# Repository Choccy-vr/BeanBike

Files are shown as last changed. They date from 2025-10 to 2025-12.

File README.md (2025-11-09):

# BeanBike

A DIY smart eBike display and controller.

## Why?

I made this because I really like eBikes; they are just fun. I have always wanted my own, but off the shelf they are way too expensive. So I thought of going the custom route, making my own controller. But then I thought, if I am really going to do this, I am not going to get some normal boring eBike I want my eBike. And that is how this came to be.

## Pictures!

### PCBs

#### Controller

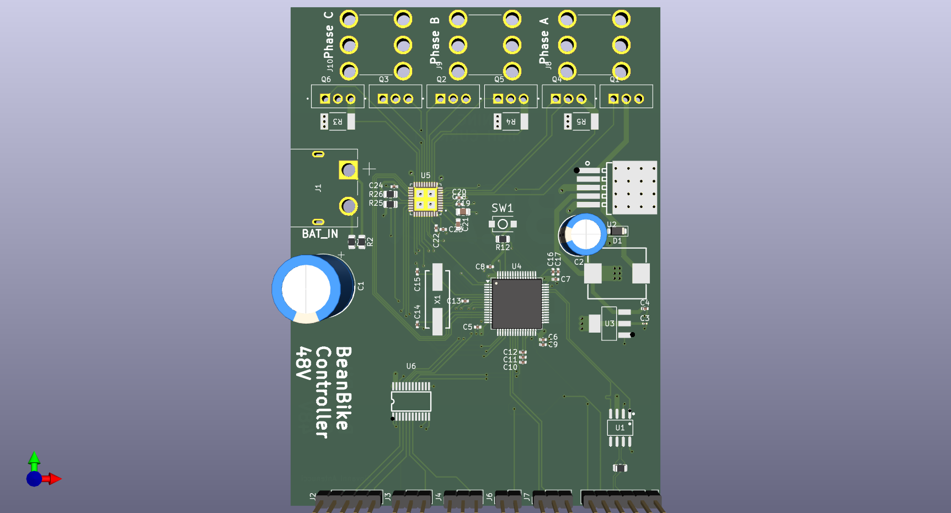
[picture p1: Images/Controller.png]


#### Display

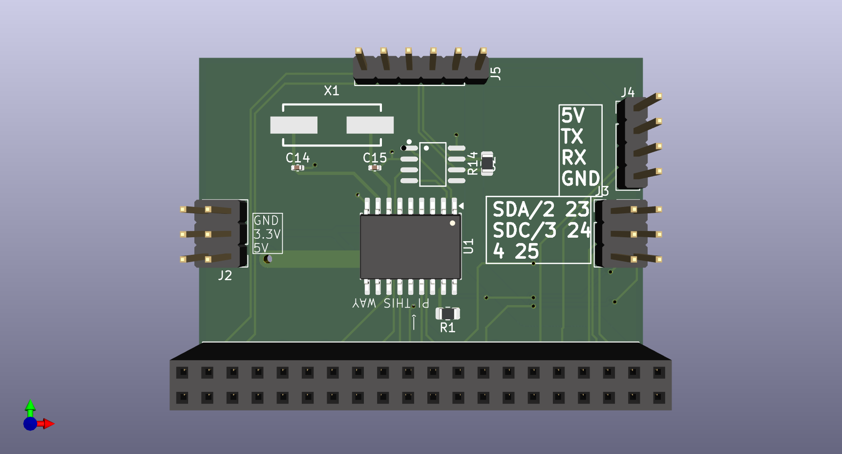
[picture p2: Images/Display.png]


## BOM

|Product Name |Product Description |Product Link |Product unit price|Product amount|Product Cost|Total (Before Tax + Shipping)|Total (Without Shipping)|Total  |
|---|---|---|---|---|---|---|---|---|
|Display-PCB |PCB for display |https://jlcpcb.com/ |4.12 |5 |$20.58 |$198.40 |$212.29 |$259.05|
|2x20 Socket |Socket for Pi |https://www.digikey.com/en/products/detail/sullins-connector-solutions/SFH11-PBPC-D20-ST-BK/1990093 |1.52 |1 |$1.52 | | | |
|2x3 Header |Expansion Pins |https://www.digikey.com/en/products/detail/sullins-connector-solutions/PBC03DAAN/861061 |0.58 |2 |$1.16 | | | |
|Display |Display for eBike |https://www.waveshare.com/product/displays/lcd-oled/lcd-oled-2/3.5inch-480x800-lcd.htm |44.99 |1 |$44.99 | | | |
|Mini-HDMI to HDMI Cable|HDMI cable for display |https://www.aliexpress.us/item/3256809615077123.html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 |1.99 |1 |$1.99 | | | |
|Micro USB to USB C |USB cable for display |https://www.amazon.com/DteeDck-Adapter-Braided-Charging-Transmission/dp/B0BD36TZBK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 |5.49 |1 |$5.49 | | | |
|Controller-PCB |PCB for controller |https://jlcpcb.com/ |11.77 |5 |$58.87 | | | |
| | | | | | | | | |
|CSS2H-2512R-1L00F |Shunt Resistors |https://www.digikey.com/en/products/detail/bourns-inc/CSS2H-2512R-1L00F/6023764 |1.27 |3 |$3.81 | | | |
| | | | | | | | | |
|PAS sensor |Pas Sensor |https://www.aliexpress.us/item/3256808182150916.html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 |1.99 |1 |$1.99 | | | |
|Throttle sensor |Twist Throttle Handle |https://www.aliexpress.us/item/3256806514034716.html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 |1.99 |1 |$1.99 | | | |
|Brake sensor |Brake/shut off sensor |https://www.aliexpress.us/item/3256805985764030.html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 |5.9 |1 |$5.90 | | | |
|MOSFET Heatsinks |Heatsink for MOSFETs |https://www.aliexpress.us/item/3256803892794950.html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 |0.2 |10 |$1.99 | | | |
|M8 Connector 2P |Connector for brake sensor |https://www.aliexpress.us/item/3256805115817349.html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 |2.97 |1 |$2.97 | | | |
|M8 Connectors 3P |Connectors for PAS and Throttle|https://www.aliexpress.us/item/3256805115817349.html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 |1.75 |4 |$6.99 | | | |
|M8 Connector 6P |Connector for Display |https://www.aliexpress.us/item/3256805115817349.html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 |3.46 |1 |$2.97 | | | |
|MOSFETs |MOSFETs |https://www.digikey.com/en/products/detail/infineon-technologies/IRFB4110PBFXKMA1/22157630 |3.06 |6 |$18.36 | | | |
|Capacitor 680uF |big cap for controller |https://www.digikey.com/en/products/detail/chemi-con/EKZN630ELL681MK30S/4843904 |1.53 |1 |$1.53 | | | |
|Capacitor 330uF |big cap for controller |https://www.digikey.com/en/products/detail/rubycon/25ZLJ330M8X11-5/3134207 |0.54 |1 |$0.54 | | | |
|Screw Terminal |Phase Connector |https://www.digikey.com/en/products/detail/keystone-electronics/8196/316832 |1.24 |3 |$3.72 | | | |
|Ring Connector |Phase Wire connector |https://www.digikey.com/en/products/detail/molex/0191930245/1952714 |0.53 |3 |$1.59 | | | |
|GPS module |GPS module |https://www.aliexpress.us/item/3256806636967867.html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|6.39 |1 |$6.39 | | | |
|M8 Connector 5P |Connector for ENCODER |https://www.aliexpress.us/item/3256805115817349.html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 |3.06 |1 |$3.06 | | | |

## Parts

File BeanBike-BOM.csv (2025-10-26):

Product Name | Product Description | Product Link | Product unit price | Product amount | Product Cost | Total (Before Tax + Shipping) | Total (Without Shipping) | Total | Estimated Total with GPS
Display-PCB | PCB for display | https://jlcpcb.com/ | 0.64 | 5 | $3.20 | $188.25 | $201.43 | $235.39 | $260-270
2x20 Socket | Socket for Pi | https://www.digikey.com/en/products/detail/sullins-connector-solutions/SFH11-PBPC-D20-ST-BK/1990093 | 1.52 | 1 | $1.52
2x3 Header | Expansion Pins | https://www.digikey.com/en/products/detail/sullins-connector-solutions/PBC03DAAN/861061 | 0.58 | 2 | $1.16
Display | Display for eBike | https://www.waveshare.com/product/displays/lcd-oled/lcd-oled-2/3.5inch-480x800-lcd.htm | 44.99 | 1 | $44.99
Mini-HDMI to HDMI Cable | HDMI cable for display | https://www.aliexpress.us/item/3256809615077123.html?curPageLogUid=s5fbXvPEQDyt | 1.99 | 1 | $1.99
Micro USB to USB C | USB cable for display | https://www.amazon.com/DteeDck-Adapter-Braided-Charging-Transmission/dp/B0BD36TZBK | 5.49 | 1 | $5.49
Controller-PCB | PCB for controller | https://jlcpcb.com/ | 6.96 | 5 | $34.80
Controller-PCBA | PCBA for controller PCB | https://jlcpcb.com/ | 29.2 | 2 | $58.40
CSS2H-2512R-1L00F | Shunt Resistors | https://www.digikey.com/en/products/detail/bourns-inc/CSS2H-2512R-1L00F/6023764 | 1.27 | 3 | $3.81
ESP32-WROOM-32E-N8 | Microcontroller for controller | https://www.digikey.com/en/products/detail/espressif-systems/ESP32-WROOM-32E-N8/13159522 | 5.28 | 1 | $5.28
PAS sensor | Pas Sensor | https://www.aliexpress.us/item/3256808182150916.html?mp=1 | 1.99 | 1 | $1.99
Throttle sensor | Twist Throttle Handle | https://www.aliexpress.us/item/3256809866650629.html?curPageLogUid=YqcZ7PjFSbH2 | 4.8 | 1 | $4.80
Brake sensor | Brake/shut off sensor | https://www.aliexpress.us/item/3256805985764030.html?curPageLogUid=UFPqvqSYBL2c | 5.9 | 1 | $5.90
MOSFET Heatsinks | Heatsink for MOSFETs | https://www.aliexpress.us/item/3256803892794950.html?curPageLogUid=eevL79xpdQiV | 0.2 | 10 | $1.99
M8 Connector 2P | Connector for brake sensor | https://www.aliexpress.us/item/3256805115817349.html?mp=1 | 2.97 | 1 | $2.97
M8 Connectors 3P | Connectors for PAS and Throttle | https://www.aliexpress.us/item/3256805115817349.html?mp=1 | 1.75 | 4 | $6.99
M8 Connector 6P | Connector for Display | https://www.aliexpress.us/item/3256805115817349.html?mp=1 | 3.46 | 1 | $2.97

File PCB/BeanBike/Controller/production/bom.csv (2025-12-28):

Designator | Footprint | Quantity | Value | LCSC Part #
C1 | CP_Radial_D12.5mm_P5.00mm | 1 | 680uF 63V
C10, C12, C13, C16, C5, C6, C7, C8 | 0402 | 8 | 100nf | C1525
C11, C17, C20, C22, C23 | 0402 | 5 | 1uF | C52923
C14, C15 | 0402 | 2 | 30pF | C1570
C18, C24 | 0402 | 2 | 0.1uF | C1525
C19 | 0805 | 1 | >10uF | C45783
C2 | CP_Radial_D8.0mm_P3.50mm | 1 | 330uF 25V
C21 | 0603 | 1 | 47nF | C1622
C3 | 0201 | 1 | 22uF | C59461
C4 | 0402 | 1 | 10uf | C15525
C9 | 0402 | 1 | 4.7uF | C1569
D1 | D_SOD-123F | 1 | D | C64898
D10 | D_SMA | 1 | 3.3v Zener | C19077475
D2, D4, D5, D6 | 0603 | 4 | LED | C2286
D3 | 0805 | 1 | LED | C2297
D7 | 0603 | 1 | LED | C2296
D8 | 0603 | 1 | LED | C2290
D9 | D_SMA | 1 | 5v Zener | C19077477
F1 | FUS_RKEF300_TYCO_TYC | 1 | 5v Polyfuse
F2 | FUSE_MF_R065_2_BRN | 1 | 3.3v Polyfuse
J1 | MountingHole_3.2mm_M3_Pad_Via | 1 | XT60 +
J10 | KEYSTONE_8196 | 1 | PHASE C
J11 | MountingHole_3.2mm_M3_Pad_Via | 1 | XT60 -
J2 | PinHeader_1x05_P2.54mm_Vertical | 1 | Conn_01x05_Pin
J3 | PinHeader_1x03_P2.54mm_Vertical | 1 | Throttle Conn
J4 | PinHeader_1x03_P2.54mm_Vertical | 1 | PAS Conn
J5 | PinHeader_1x06_P2.54mm_Vertical | 1 | Display Conn
J6 | PinHeader_1x02_P2.54mm_Vertical | 1 | Brake Conn
J7 | PinHeader_1x06_P2.54mm_Vertical | 1 | ST-Link-Debug
J8 | KEYSTONE_8196 | 1 | PHASE A
J9 | KEYSTONE_8196 | 1 | PHASE B
L1 | IND-SMD_L11.6-W10.1 | 1 | CYA1040-33UH | C6364680
Q1 | TO254P1050X476X2020-3 | 1 | PHASE A HIGH
Q2 | TO254P1050X476X2020-3 | 1 | PHASE B HIGH
Q3 | TO254P1050X476X2020-3 | 1 | PHASE C HIGH
Q4 | TO254P1050X476X2020-3 | 1 | PHASE A LOW
Q5 | TO254P1050X476X2020-3 | 1 | PHASE B LOW
Q6 | TO254P1050X476X2020-3 | 1 | PHASE C LOW
R1, R12 | 0805 | 2 | 10k | C17414
R10, R6, R8, R9 | 0805 | 4 | 15k | C17475
R11, R13 | 0805 | 2 | 1k | C17513
R14 | 0805 | 1 | 120 | C17437
R2 | 0805 | 1 | 180k | C17501
R25, R26 | 0805 | 2 | 73k | C17819
R3, R4, R5 | RES_1L00x_BRN | 3 | CSS2H-2512R-1L00F | C4175647
R7 | 0805 | 1 | 330 | C17630
SW1 | SW-SMD_L3.9-W3.0-P4.45 | 1 | SW_Push | C720477
U1 | SOIC-8_L4.9-W3.9-P1.27-LS6.0-BL | 1 | SN65HVD230DR | C12084
U2 | PG-TO-263-5_L10.2-W8.7-P1.70-LS14.4-BR | 1 | TD1501HS50 | C134490
U3 | SOT-223-3_L6.5-W3.4-P2.30-LS7.0-BR | 1 | AMS1117-3.3 | C6186
U4 | LQFP-64_10x10mm_P0.5mm | 1 | STM32G473RETx | C730120
U5 | QFN50P600X600X80-41N | 1 | DRV8353SRTAT | C2150480
U6 | TSSOP-24_L7.8-W4.4-P0.65-LS6.4-BL | 1 | SN74LVC4245APWR | C7859
X1 | CRYSTAL-SMD_L11.5-W4.8-LS12.7 | 1 | X49SM8MSD2SC | C12674

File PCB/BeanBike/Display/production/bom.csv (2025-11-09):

Designator | Footprint | Quantity | Value | LCSC Part #
C14, C15 | 0402 | 2 | 30pF | C1570
J1 | PinSocket_2x20_P2.54mm_Vertical | 1 | Pi 0 2W
J2 | PinHeader_2x03_P2.54mm_Vertical | 1 | Power Conn
J3 | PinHeader_2x03_P2.54mm_Vertical | 1 | Data Conn
J4 | PinHeader_1x04_P2.54mm_Vertical | 1 | GPS/DEBUG
J5 | PinHeader_1x06_P2.54mm_Vertical | 1 | Display Conn
R1 | 0805 | 1 | 10k | C17414
R14 | 0805 | 1 | 120 | C17437
U1 | SOIC-18W_7.5x11.6mm_P1.27mm | 1 | MCP2515-xSO | C15193
U2 | SOIC-8_L4.9-W3.9-P1.27-LS6.0-BL | 1 | SN65HVD230DR | C12084
X1 | CRYSTAL-SMD_L11.5-W4.8-LS12.7 | 1 | X49SM8MSD2SC | C12674

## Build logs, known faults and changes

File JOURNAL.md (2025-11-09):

<!--
  ===================    !!READ THIS NOTICE!!   ====================
  DO NOT edit this file manually. Your changes WILL BE OVERWRITTEN!
  This journal is auto generated and updated by Hack Club Blueprint.
  To edit this file, please edit your journal entries on Blueprint.
  ==================================================================
-->

## 10/10/2025 5 PM - Started KiCad Project  

Didn't really do a lot, just started the KiCad Project and labeled all the MCU pins for the controller.



Well, pretty much it, but I need 250 characters, so I will talk about blueprint. I kinda am liking it, it is obviously a continuation of Highway, but I like it. Ngl kinda feels unoriginal, but I still like it. 

It is basically Highway, but with some parts of SoM and more refined.  

## 10/10/2025 8 PM - Finished V1 Power Circuit  

I basically made the schematic for the power supply.

Most of the time was spent researching and seeing what I had to do to make sure it is safe and everything gets what it wants. I am debating getting the Power on a different board, but I don't think I will.
But now I have battery level, 3.3v (MCU), 5v (display), 12v (misc like lights). 
I made a more complex circuit, but then I realized eBike batteries already have a BMS 😭 so I got rid of it.
So far, kinda liking this, but I am dreading the day I have to make a case, especially waterproof :(  

## 10/10/2025 9 PM - Added Connectors  

I went through and did all the tedious work of creating the connectors. 

I was also thinking about the features I am going to add specifically for anti-theft. I want to have enough smart anti-theft features that you don't need to lock your bike up. So I will have things like PIN, Phone detection to make sure you can ride it. To make sure that if you do try to steal it, you won't be able to, I will lock the motor, start an alarm, pretty much cut power, other than to the anti-theft features, oh, and also GPS. So this would be effective, but thieves could still pick it up, take out the battery, and other things so I will probably still carry one around, but for those times when you forget it, then you can still be calm knowing your bike won't get stolen.  

## 10/11/2025 1 PM - Motor Controller  

I finished the Motor connection and etc.

So I used a BLDC motor IC for easy controlling and etc. Honestly I don't get why eBike controller are so expensive this seems down right resonable.
When I brake it will now automatically cut power to the motor no matter what (Hard wired) and I can control it with firmware too. So now I am going to go through and finish a few things then I will test it in a simulation and then I should be good to go to the PCB.  

## 10/11/2025 4 PM - Footprints  

I hate selecting footprints; let's make that clear right now, I hate it.

I ran the ERC and fixed all those problems, and I moved to selecting the footprints. I got a list on Digi-Key for all my parts, but I hate this still. A big, big problem I am facing right now is that I need 3 buck converters for 3.3v, 5v, and 12v. Someone suggested going from 12v to 5v then to 3.3v so I will try that.  

## 10/11/2025 7 PM - 48v -> 24v  

Ok for the past 2 hours I have been working on the buck converters.

Tell me why it is so hard to just go down to a lower voltage doesn't make sense but whatever. I spent1.5 hours trying to make my own but the n I came across a actual life saver [webench.ti.com/power-designer](webench.ti.com/power-designer). I got done my 24v converter and now the rest  

## 10/11/2025 8 PM - Finished V1 Schematic  

I finally finally finished V1 of my motor controller!

You know how earlier I said I don't get why motor controllers are so expensive? Yeah, I take that back. I finished all the conversions and now have 24v, 12v, 5v, and 3.3v available to me, all at around 2.5A. I thought the inductors would've made this huge, but ehh, I am estimating around 100mm by 90mm. Then, to top it all off, I did footprints my favorite.  

## 10/12/2025 3 PM - Started PCB  

I started on the PCB.

I started by grouping the components into sections of the board, like one group for power, one for motor, one for connectors, and one for the MCU. I then combined them into a compact layout, drew my edge cuts, and started plotting traces. I have done most of the power, and now I am on data. The board will have 4 layers, front and back for power, and the middle layers for data. After I finish it, I will probably ask someone to review it because this is my first PCB with a lot of current, and I need it to be safe.  

## 10/12/2025 9:29 PM - Finished V1 PCB  

I finished routing all the PCB, and it should be good!

To be honest, I am not that confident, so that is why I am getting it reviewed by someone a lot smarter than me. This feels really nice to get done. I would say this is the hardest part; it should all be smooth sailing from here. And best of all, software is next! Oh, also, I forgot to run to DRC, guess I have to do that :( I really hate all the repetitive work of making PCBs like it is fun until you get to that part.  

## 10/12/2025 9:48 PM - Quick Update: DRC & Silkscreen  

Quick update: I fixed DRC violations and added silk screen text.  

I don't think I am done with it completely. I still have to add all the part numbers, but really, I already have them picked out; I just need to put them in and generate the BOM and Gerbers. It is easy but repetitive. Welp, see you then  

## 10/14/2025 - PCB v2  

I have done alot of research and getting feedback.

I have gotten feedback on my PCB and how not to burn down my house. I need to majorly increase the track width but I have decided to just up my board to 6 layers and it would be like this. Back:Solid GND In4:PWR_MOTOR then the rest is yet to be decided but that is what is new. Then in v1 signals were being passed from one area to another (mostly at connectors) so I am fixing that. I felt it would be easier to just redo the routing and as a perk I can make it neater.  

## 10/15/2025 - Layout PCB v2  

I have laid out all of PCB v2 this time, taking a lot more care into it.

I have decided to omit the 24V and 12V lines. Really, I had no use for them other than lights, but after seeing how expensive wired-in lights are, I decided against it. The PCB is split into 3 parts now: MCU, Power, and Motor. I am still deciding whether to arrange it vertically or more horizontally, but I am thinking vertically.  

## 10/16/2025 6 PM - Issues  

Well, I laid out my PCB v2, and it's all good, but there is an issue.

So I laid out my PCB, it was all nice and neat, but ... I just now realized that the chip I was using the DRV8308 does not support 48v :(. So I have to replace it. I am replacing it with the DRV8353. It is a newer chip and supports 48v. But I really do not want to change everything.  

## 10/16/2025 9 PM - Updated Motor IC  

So after a lot, I finally got the motor IC all updated.

It was a lot, but I think I finally have this all down, and it feels so nice. One good thing happened, though I had the MOSFETs mixed up, so that would not have been good. I rearranged the GPIOs to make it fit a lot better. I also got to get rid of the level shifters, and I feel it is a lot less complex.  

## 10/18/2025 - PCB v2  

I routed a placed everything on PCB v2 and it should be finished.

Been a while. But I finished everything on PCB v2 (except silkscreen). I placed all the new components updated it and all nice and neat. I added copper fills for connecting my high-power things so I don't have to worry about big traces. But anyway, now I am getting it reviewed once again to make sure it is very good.  

## 10/19/2025 11 AM - Finish PCB v2  

I had a problem with my PCB, but I fixed it, and now v2 is officially finished.

In my PCB, there were some isolated copper islands, so I had to fix that by re-routing some of the PCB. This should be the actual PCB that I send to JLC PCB. Now I'm going to make the firmware, and it shouldn't be too hard. Altough I have never interacted with a SPI device without a library so that will take a bit.  

## 10/19/2025 3 PM - DRV8353 implementation  

I am finally working on firmware!

Right now, I am working on the DRV8353 implementation. I have Fault detection working. For everywhere you see uart.sendData(), that is me sending data to my display (the smart thing) to see what it will decide to do with it. At first, I was a little nervous because I had never read/write raw registries from SPI, but it is kind of easy. Oh, and I also set up an interrupt on the FAULT pin to make sure I catch all faults instantly. Next up is Driver Control.  

## 10/19/2025 8 PM - Finished DRV8353 implementation  

I finished the DRV8353 implementation.

Note, this does not mean that my controller firmware is done, just that the code to interface with the DRV8353 is done. Anyway, I added a bunch of functions to control all the different registries. Next, I have to make the motor control code (PAS, Cruise Control, actually sending PWM signals, getting motor speed, etc.).

## 10/20/2025 - More Firmware  

Yay, more Firmware writing

Anyway, let's first talk about #lounge exploding rn first time it has seen use in forever. Also, why did AWS go down? It was so annoying, I could do basically nothing. But back to my project, I basically just wrote a bunch of code for the firmware. That is it, I am tired and want to go to bed gn.  

## 10/21/2025 - *Finished Firmware  

So I finished the firmware!!

* Well, I sort of did. 
Software is never finished; I can just keep adding and adding, and I plan to. This is just it has enough that it will work, I can always change it. That is the great thing about software. Anyway some of the calculations may be off but this is because I don't have the motor or bike to base it off of. I am going to keep adding to it, but as of now, to the display!

## 10/22/2025 5 PM - Research & Schematic  

So I researched for a while, and I landed on the Pi Zero 2 W.

Most of the time spent on this journal was researching, I couldn't choose what to run my display on, and a display. I needed a ~3.5in display, and SPI just wouldn't really work, so the next abundant option was DSI. But another problem arose, the board I was planning on using, the Pi Zero 2 W, doesn't have DSI. So I was contemplating using a Compute module or using an HDMI display with the zero. I decided to use an HDMI display, even though it is a bit more expensive, it is easily swappable, so if anything ever goes wrong. This PCB isn't a complicated one, not supposed to be, mainly just supposed to organize my board.

## 10/22/2025 7 PM - Display PCB  

So I finished the Display PCB

Again, just re-stating this is not supposed to be a complex PCB, just something to better organize my screen. So with that out of the way, now it is on to the most important part of this, making the customized OS. This custom OS will let me strip down to just what I need, further decreasing boot time, and as a bonus, it makes it seem more professional.  

## 10/25/2025 11 AM - Bike App  

I started work on the Bike app

I think it looks really good. I am just working on the UI now, and functionality will come later. Also, quick update on this, I am really starting my YSWS rn and don't know if I will be able to finish this. I will try, but I might have to cut some things out.  

## 10/25/2025 2 PM - Way too many variables  

I have way way way to many variables.

Like it is absurd to creater this UART script it took 2 hrs of mindless copy and pasting. Anyway I am happy that it is done. I think that I still have to change a few things to make everything work all nice. I have to add a few more things and then v1 of the app will be done. I think since I am starting to get super busy I am going to strip out alot of what I planned but it still would be quite a advanced eBike and then through OTA updates keep adding.

## 10/25/2025 4 PM - Finish up Software  

I finished up the software. 

So I finished up the rest of the app and fixed a few things with the controller firmware. Then I built the firmware, and I tried to build the app turns out you need to be on Linux. So I tried macOS turns out that doesn't count as Linux, so I had to go into Ubuntu and build it there. Surprisingly more complicated than I thought. Anyway, I have it all built, and now I have to get it ready for shipping.

## 10/25/2025 11 PM - Finishing Things Up  

This is by far the most time I have spent on one journal.

This journal was a long one. I got everything ready for shipping. I made all my gerbers and BOMs for my PCB changed a good amount of my parts, just so I can get the PCBA cost down. README, organizing, and more. Always hated this part of hardware. It is always so boring and long. Anyway, I got some feedback that my project is at most a tier 2 and maybe a tier 3. That is not good at all. So I might add a GPS module, one problem with that is that although it will increase the price, something I am already over the tier 2 budget.

## 10/26/2025 - Finished  

Ok so I have finished it! I really wanted to get in GPS but I don't have the budget :(. I really need this to be a tier 2 project at least or some way to get the extra budget I am $35.39 over (which isn't that much) but I don't think I could cover that. I included the estimated price with GPS too just in case there is some way to get it covered. maybe by some miracle I can get tier 1 or some way to get the extra funds covered. I also researched the GPS module if I do get GPS I am going for the MAX-M10M-00B cheapest one I could find that is still well supported and accurate.


## 10/30/2025 - Research Research Research  

Some say research is the thief of all joy.

So, I need to narrow my PCB down to 4 layers, but after **researching**, I noticed a VESC project. Basically, it is an open-source project for motor controllers, firmware, etc., which is great. However, the hardware schematics haven't been updated for a while. Also, while I would know that it would work well, I don't know; something is just wrong with it. It kind of defeats the purpose of doing all of this by myself. So I will probably not copy off of it, but I will take inspiration just to make sure my board is ready for this. Also, I think maybe I might switch to an STM32. I don't like it, but it does make a lot of sense for this project, and I think it is cheaper and smaller than an ESP.  

## 10/31/2025 - Project Journal?  

Well, I finally did it. I started a project journal.


As my projects get more and more advanced, I really need somewhere to document my research, my notes, etc. I am actually finding it very beneficial, plus it makes it seem more professional. Anyway, a lot of stuff happened in this session. I really started to research all of the different things I am doing. Like for the MCU, I am moving away from the ESP32 to the STM32G4. And still researching this, but switching from UART to CAN. I am very excited about it seems like it is a vast step up from UART tbh, no clue why I didn't start with it, mostly because the ESP doesn't have that, and I didn't know a lot about it. Last remark paper has its limits. I want an iPad so bad  

## 11/1/2025 1 PM - Last Bit of Research  

Well, I think I have done enough research to start working on the schematic.

I have chosen new ICs for the buck converters. The LM2596HVS is for 48v to 5v. The TPS5430DDAR is for 5v to 3.3v. These, I feel, are going to help a lot. First of both are an all-in-one package, which is super nice. Then the LM2596HVS can do 3A, so that would also be nice. Both are also a lot less money. More went into it, but that was an overview. So here we go!  

## 11/1/2025 2 PM - PCB v3 Schematic  

I started work on PCB v3!

So I got rid of pretty much all power items to replace them. 5V was pretty easy; I needed an external inductor, which I thought I got rid of, but fine. Also, I changed to TD1501HS50. Then, for 3.3,v I was going to use a buck converter, but I realized I could just use an LDO. So I picked the AMS1117-3.3, and that circuit is very simple. I am now going to the STM32!

## 11/1/2025 8 PM - Simple FOC & Resaerch!  

I recently came across a project called [Simple FOC](https://github.com/simplefoc/Arduino-FOC).

This looks like it will be super nice for me and work pretty easily with my Motor IC and STM32. I also came across this YouTuber [Great Scott](https://www.youtube.com/@greatscottlab). I watched a good amount of his videos to get a better grasp on FOC and Electric Motors.  

## 11/4/2025 - iPad!!!  

It has been a while, but great news, I got an iPad!!!!!


Facebook Marketplace is a lifesaver. So instead of having a physical notebook, I can have a digital one! So I transferred everything from my paper notebook to my iPad. 
I also set up the STM32 (at least the power pins) and researched more into how to develop with an STM32. I am very new to the whole STM32 thing. I might need to add an external oscillator, but idk. 


## 11/5/2025 - STM32  

I am still working on the STM32.

I am going a lot slower now, but still making good progress. I have set up all the special pins on the STM32, and now it is completely configured, except for the remaining general-use pins. Turns out that even though the STM32 supports CAN, you still need a transceiver, so  I added that.

## 11/6/2025 - Finished MCU  

Well, I finally finished the MCU part of the schematic.

Pretty much, I just added all those Global Labels and also fixed a few things. Now all that is left for the schematic is the motor driver, but I just need to attach those pins to the new MCU pins. Oh, also, I made a nice little table on my iPad to tell me what each pin does and whether it is in use or not. I am fast approaching the PCB layout, and to say the least, I am scared but also excited.

## 11/7/2025 4 PM - Almost!  

I am finally almost done with the schematic!

So I have pretty much everything done, but ... I learned that supposedly you need bulk capacitors for the motor phases, so yay. Also, I have to add a few things to stop the current from reversing. Then, after all that, it goes on to my least favorite part, Footprints and LCSC IDs!

## 11/7/2025 5 PM - Schematic v3 Done!  

I finally finished v3 of the schematic.

So I changed a few things first, and probably most importantly, I had my MOSFETs wired wrong, which is embarrassing. I also didn't understand my driver's datasheet and wired VDRAIN wrong, but fixed that. So I think that is it, and time to go to footprints.  

## 11/7/2025 10 PM - Finished footprints v3 & Cost Optimization  

I finished the footprints, hopefully for the last time.

I hate footprints so much; it is so boring and tedious, but I got it out of the way. So, along with setting all the footprints, I also put in the LCSC ID for my BOM. I made sure to get all basic items. I think only two parts aren't basic, and they are the STM and the DRV. But onto the PCB. 
This is going to be fun.

## 11/8/2025 12 PM - Fixed a few things on the schematic  

So I forgot a part on the schematic, but I fixed it. 

I forgot to connect my connector data pins to my STM, so I had to find out what my sensors output (PWM, GPIO, etc.) Then I needed to use a level shifter to get them down to 3.3V LOGIC. I saved and updated everything, and now we have all of our components on the PCB, and we have to lay them out.

## 11/8/2025 4 PM - Started PCB v3  

I started PCB v3 and laid everything out

The amount of care and precision I am putting into this PCB revision is insane. Anyway, I grouped up all the different components and arranged them to make sure it looks good, follows the datasheet, and is clean. Then I routed some pins. I made a few minor adjustments to the schematic, but nothing major.

## 11/8/2025 10 PM - Almost there.  

I actually locked in so hard and am bascially done my PCB.

I only have three connections left and that is the Motor Phases. I seprated the Encoder from the actual motor for better compatiblity of diffrent motors. I took a lot of time and care and got the PCB routed all nice and neat and it looks great. Only thing now are the stupid Phases. I am moving to a Ring connector and why in the world is it so incredibly hard to get a footprint for it. That will be tommorow's job.

## 11/9/2025 9 AM - Finished PCB v3 & Cost optimization  

I finally finally finished hopefully the last PCB version

I really like how this came out it actually looks professional. Anyway I connected the remaining 3 lines. I ended up going with a ring connector reason being for higher motors like 2000w they use that and it is a better connector. I also shrnk the board just so I can be under 100mm so I don't have to pay extra! Now I am going to go check how much this is going to cost.

## 11/9/2025 1 PM - Finished Display v3. Low Cost  

The display board is done!!!!

You might notice there is a lot more on here than before and you would be right. I had to add a CAN controller and transiever. I also added a header to the side for DEBUG or a GPS module. Do you know what is funny the price of both of these boards combined is less then what the controller use to cost and I added stuff!

## 11/9/2025 2 PM - FINISHED & More Cost Optimization  

I finally finished v3 of BeanBike.

After a long time, this is done. I am not completely done; I still have to build and fix what may come up. I updated the BOM pictures wrl etc. I also spent some time further cost-optimizing it. I actually got lower than my old version, but shipping is just so much money, and nothing I can do about that. I picked the cheapest option.

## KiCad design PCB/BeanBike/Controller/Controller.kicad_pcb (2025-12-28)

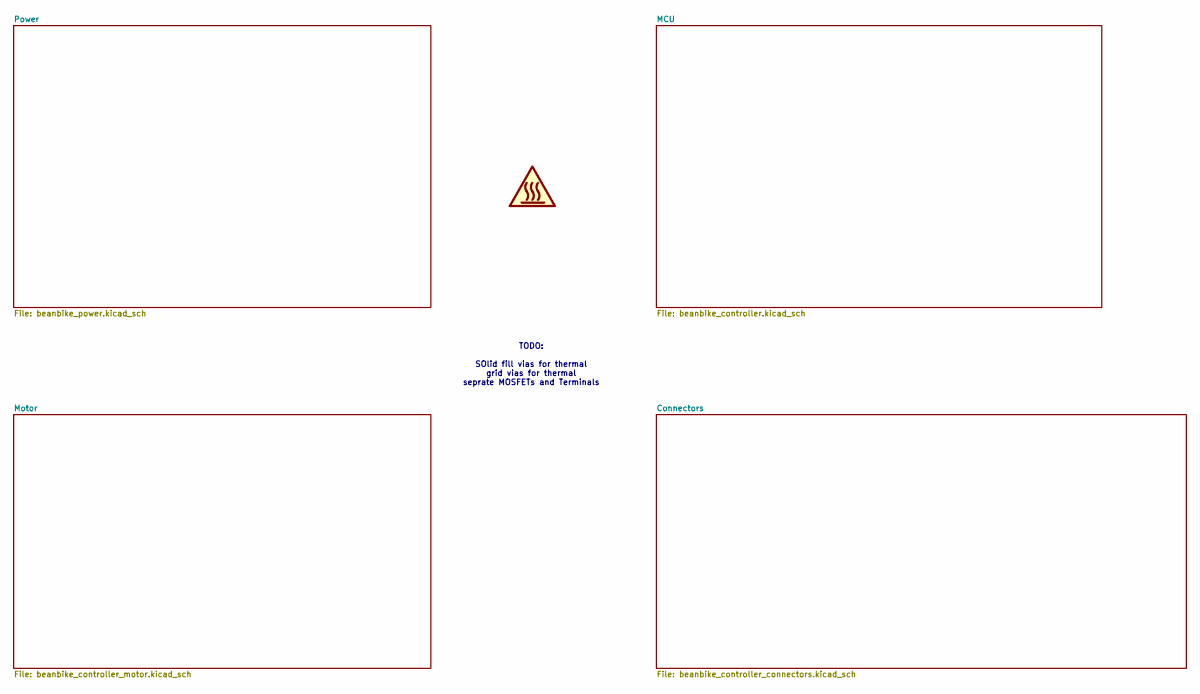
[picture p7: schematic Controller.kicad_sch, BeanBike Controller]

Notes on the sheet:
TODO: SOlid fill vias for thermal grid vias for thermal seprate MOSFETs and Terminals

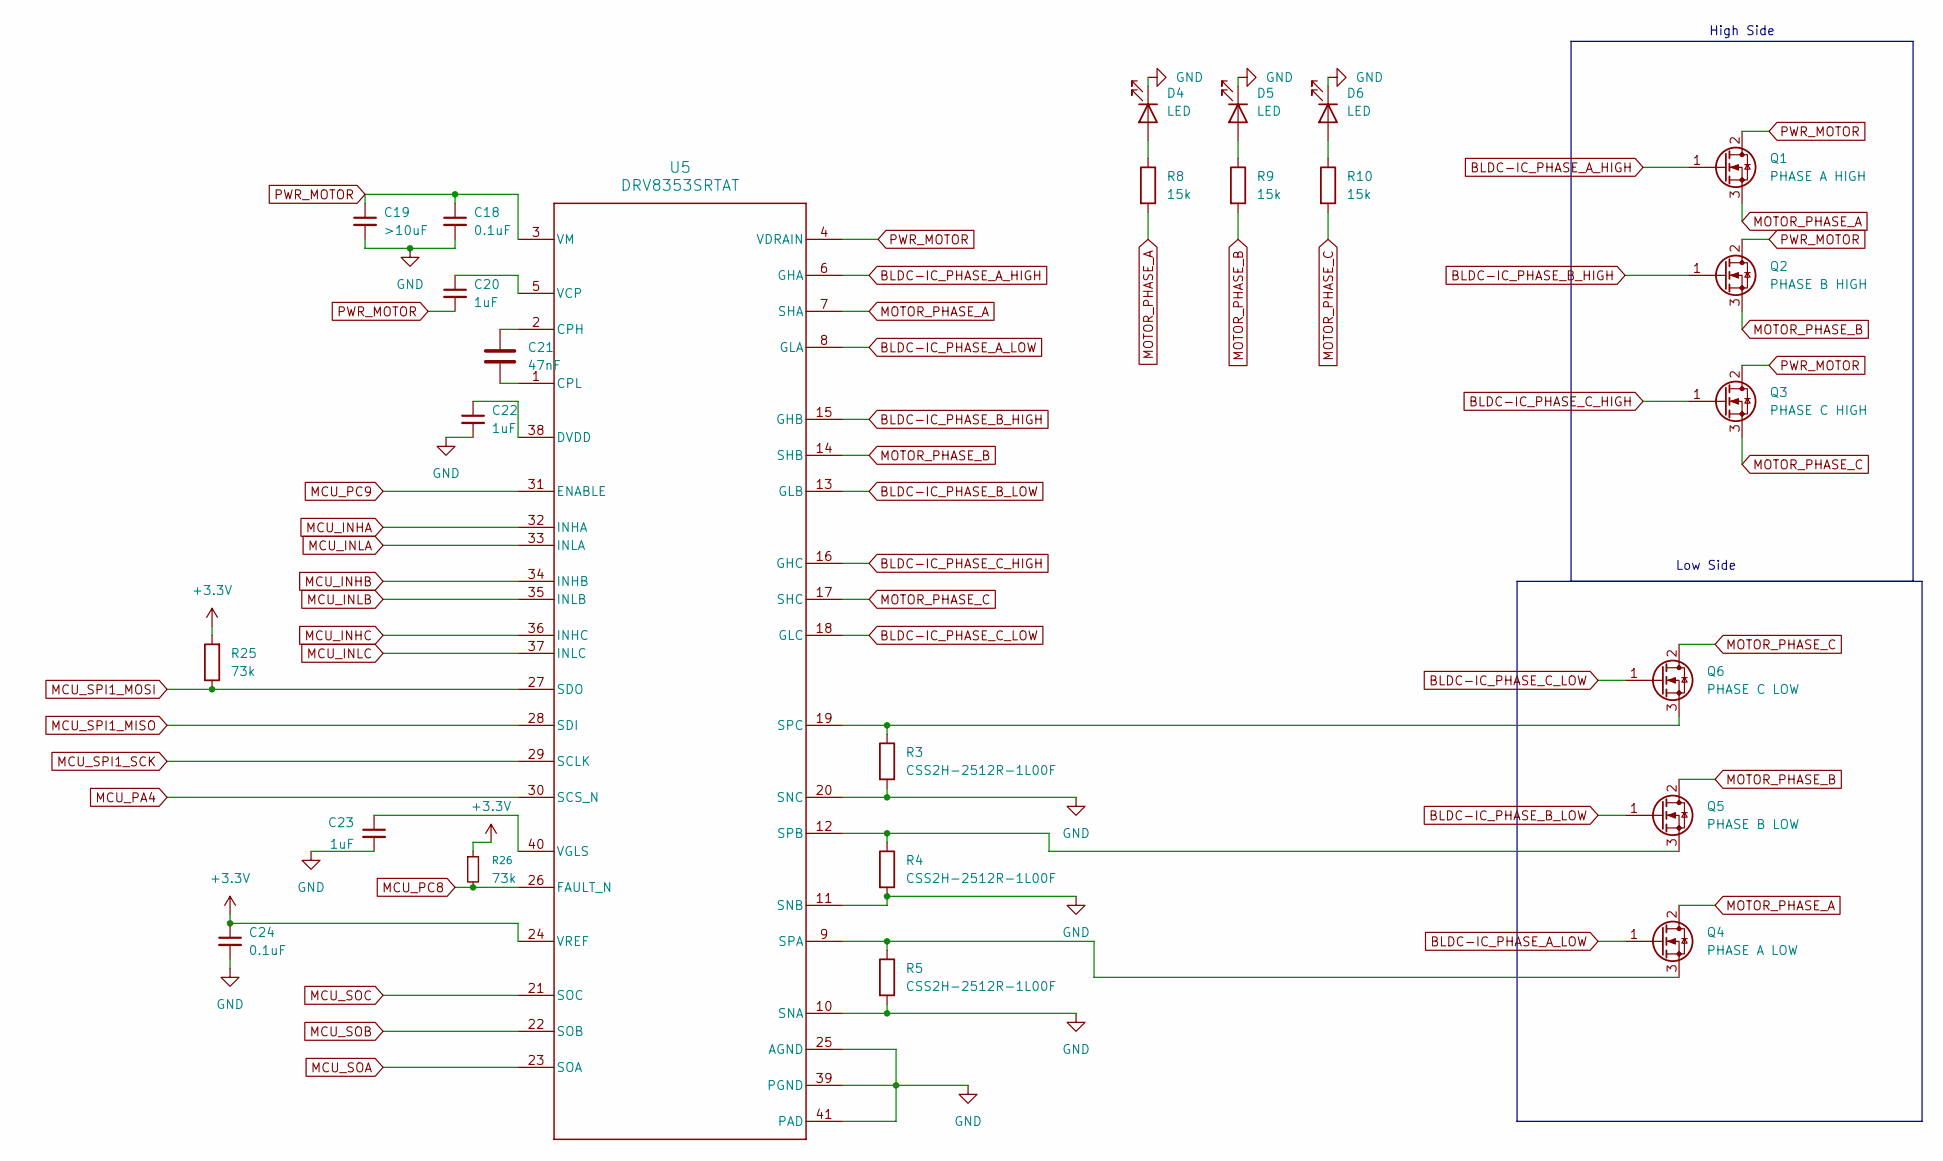
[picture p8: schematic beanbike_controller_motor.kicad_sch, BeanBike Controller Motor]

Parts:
C18, C24: 0.1uF; C_0402_1005Metric; LCSC C1525
C19: >10uF; C_0805_2012Metric; LCSC C45783
C20, C22, C23: 1uF; C_0402_1005Metric; LCSC C52923
C21: 47nF; C_0603_1608Metric; LCSC C1622
D4, D5, D6: LED; LED_0603_1608Metric; LCSC C2286
Q1: PHASE A HIGH; TO254P1050X476X2020-3
Q2: PHASE B HIGH; TO254P1050X476X2020-3
Q3: PHASE C HIGH; TO254P1050X476X2020-3
Q4: PHASE A LOW; TO254P1050X476X2020-3
Q5: PHASE B LOW; TO254P1050X476X2020-3
Q6: PHASE C LOW; TO254P1050X476X2020-3
R3, R4, R5: CSS2H-2512R-1L00F; RES_1L00x_BRN; LCSC C4175647
R8, R9, R10: 15k; R_0805_2012Metric; LCSC C17475
R25, R26: 73k; R_0805_2012Metric; LCSC C17819
U5: DRV8353SRTAT; QFN50P600X600X80-41N; LCSC C2150480

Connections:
+3.3V: C24.1, R25.2, R26.1, U5.24 (VREF); also elsewhere on the board
BLDC-IC_PHASE_A_HIGH: Q1.1 (G), U5.6 (GHA)
BLDC-IC_PHASE_A_LOW: Q4.1 (G), U5.8 (GLA)
BLDC-IC_PHASE_B_HIGH: Q2.1 (G), U5.15 (GHB)
BLDC-IC_PHASE_B_LOW: Q5.1 (G), U5.13 (GLB)
BLDC-IC_PHASE_C_HIGH: Q3.1 (G), U5.16 (GHC)
BLDC-IC_PHASE_C_LOW: Q6.1 (G), U5.18 (GLC)
BRAKE_GND: C18.2, C19.2, C22.2, C23.2, C24.2, D4.1 (K), D5.1 (K), D6.1 (K), R3.2, R4.2, R5.2, U5.10 (SNA), U5.11 (SNB), U5.20 (SNC), U5.25 (AGND), U5.39 (PGND), U5.41 (PAD); also elsewhere on the board
MCU_INHA: U5.32 (INHA); also elsewhere on the board
MCU_INHB: U5.34 (INHB); also elsewhere on the board
MCU_INHC: U5.36 (INHC); also elsewhere on the board
MCU_INLA: U5.33 (INLA); also elsewhere on the board
MCU_INLB: U5.35 (INLB); also elsewhere on the board
MCU_INLC: U5.37 (INLC); also elsewhere on the board
MCU_PA4: U5.30 (SCS_N); also elsewhere on the board
MCU_PC8: R26.2, U5.26 (FAULT_N); also elsewhere on the board
MCU_PC9: U5.31 (ENABLE); also elsewhere on the board
MCU_SOA: U5.23 (SOA); also elsewhere on the board
MCU_SOB: U5.22 (SOB); also elsewhere on the board
MCU_SOC: U5.21 (SOC); also elsewhere on the board
MCU_SPI1_MISO: U5.28 (SDI); also elsewhere on the board
MCU_SPI1_MOSI: R25.1, U5.27 (SDO); also elsewhere on the board
MCU_SPI1_SCK: U5.29 (SCLK); also elsewhere on the board
MOTOR_PHASE_A: Q1.3 (S), Q4.2 (D), R8.2, U5.7 (SHA); also elsewhere on the board
MOTOR_PHASE_B: Q2.3 (S), Q5.2 (D), R9.2, U5.14 (SHB); also elsewhere on the board
MOTOR_PHASE_C: Q3.3 (S), Q6.2 (D), R10.2, U5.17 (SHC); also elsewhere on the board
unnamed: D4.2 (A), R8.1
unnamed: D5.2 (A), R9.1
unnamed: D6.2 (A), R10.1
unnamed: Q4.3 (S), R5.1, U5.9 (SPA)
unnamed: Q5.3 (S), R4.1, U5.12 (SPB)
unnamed: Q6.3 (S), R3.1, U5.19 (SPC)
unnamed: C21.1, U5.2 (CPH)
unnamed: C21.2, U5.1 (CPL)
unnamed: C22.1, U5.38 (DVDD)
unnamed: C20.1, U5.5 (VCP)
unnamed: C23.1, U5.40 (VGLS)
PWR_MOTOR: C18.1, C19.1, C20.2, Q1.2 (D), Q2.2 (D), Q3.2 (D), U5.3 (VM), U5.4 (VDRAIN); also elsewhere on the board

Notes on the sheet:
High Side
Low Side

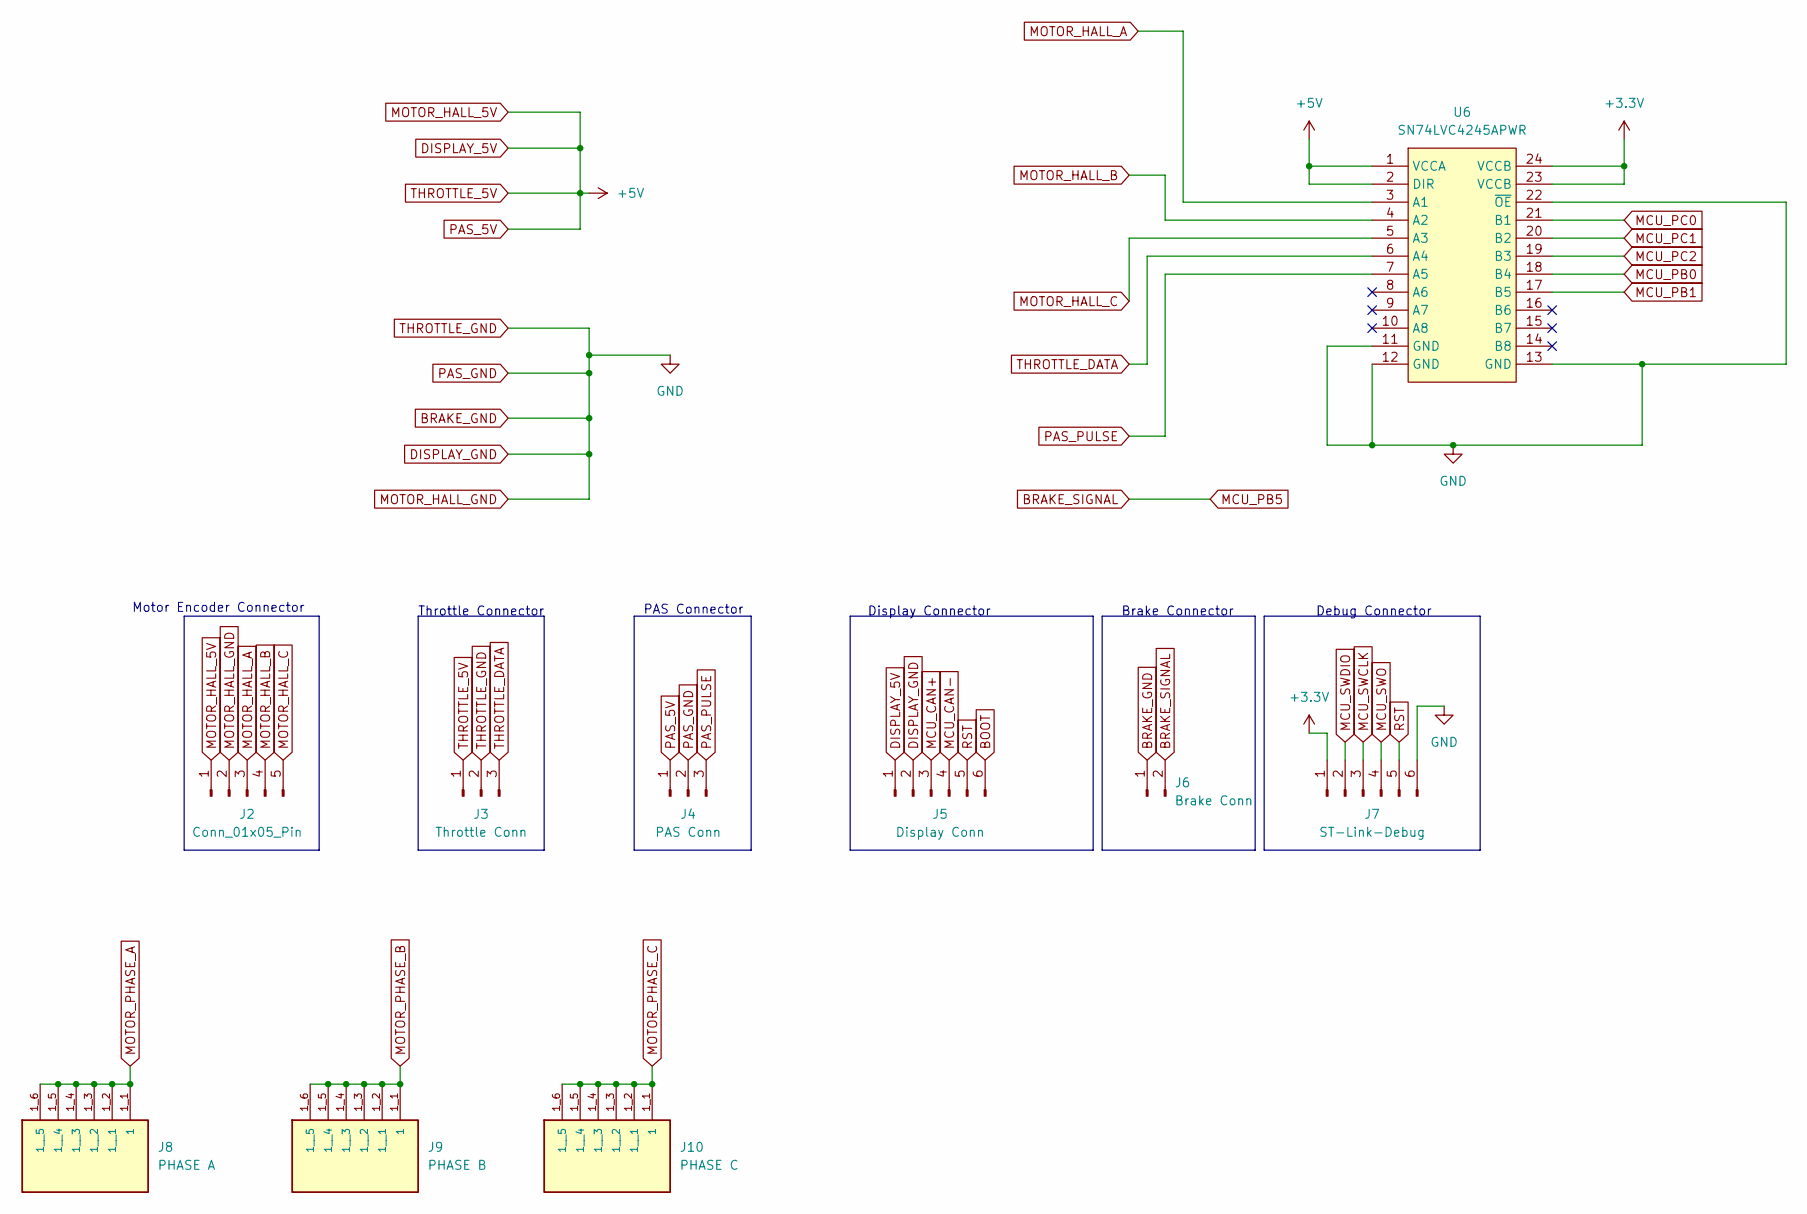
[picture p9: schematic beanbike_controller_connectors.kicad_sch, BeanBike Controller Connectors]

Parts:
J2: Conn_01x05_Pin; PinHeader_1x05_P2.54mm_Vertical
J3: Throttle Conn; PinHeader_1x03_P2.54mm_Vertical
J4: PAS Conn; PinHeader_1x03_P2.54mm_Vertical
J5: Display Conn; PinHeader_1x06_P2.54mm_Vertical
J6: Brake Conn; PinHeader_1x02_P2.54mm_Vertical
J7: ST-Link-Debug; PinHeader_1x06_P2.54mm_Vertical
J8: PHASE A; KEYSTONE_8196; PARTREV D
J9: PHASE B; KEYSTONE_8196; PARTREV D
J10: PHASE C; KEYSTONE_8196; PARTREV D
U6: SN74LVC4245APWR; TSSOP-24_L7.8-W4.4-P0.65-LS6.4-BL; LCSC Part C7859

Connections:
+3.3V: J7.1, U6.23 (VCCB), U6.24 (VCCB); also elsewhere on the board
BOOT: J5.6; also elsewhere on the board
BRAKE_GND: J2.2, J3.2, J4.2, J5.2, J6.1, J7.6, U6.11 (GND), U6.12 (GND), U6.13 (GND), U6.22 (~OE); also elsewhere on the board
BRAKE_SIGNAL: J6.2; also elsewhere on the board
DISPLAY_5V: J2.1, J3.1, J4.1, J5.1, U6.1 (VCCA), U6.2 (DIR); also elsewhere on the board
MCU_CAN+: J5.3; also elsewhere on the board
MCU_CAN-: J5.4; also elsewhere on the board
MCU_PB0: U6.18 (B4); also elsewhere on the board
MCU_PB1: U6.17 (B5); also elsewhere on the board
MCU_PC0: U6.21 (B1); also elsewhere on the board
MCU_PC1: U6.20 (B2); also elsewhere on the board
MCU_PC2: U6.19 (B3); also elsewhere on the board
MCU_SWCLK: J7.3; also elsewhere on the board
MCU_SWDIO: J7.2; also elsewhere on the board
MCU_SWO: J7.4; also elsewhere on the board
MOTOR_HALL_A: J2.3, U6.3 (A1)
MOTOR_HALL_B: J2.4, U6.4 (A2)
MOTOR_HALL_C: J2.5, U6.5 (A3)
MOTOR_PHASE_A: J8.1_1 (1), J8.1_2 (1__1), J8.1_3 (1__2), J8.1_4 (1__3), J8.1_5 (1__4), J8.1_6 (1__5); also elsewhere on the board
MOTOR_PHASE_B: J9.1_1 (1), J9.1_2 (1__1), J9.1_3 (1__2), J9.1_4 (1__3), J9.1_5 (1__4), J9.1_6 (1__5); also elsewhere on the board
MOTOR_PHASE_C: J10.1_1 (1), J10.1_2 (1__1), J10.1_3 (1__2), J10.1_4 (1__3), J10.1_5 (1__4), J10.1_6 (1__5); also elsewhere on the board
PAS_PULSE: J4.3, U6.7 (A5)
RST: J5.5, J7.5; also elsewhere on the board
THROTTLE_DATA: J3.3, U6.6 (A4)

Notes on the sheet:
Debug Connector
Display Connector
Throttle Connector
PAS Connector
Brake Connector
Motor Encoder Connector

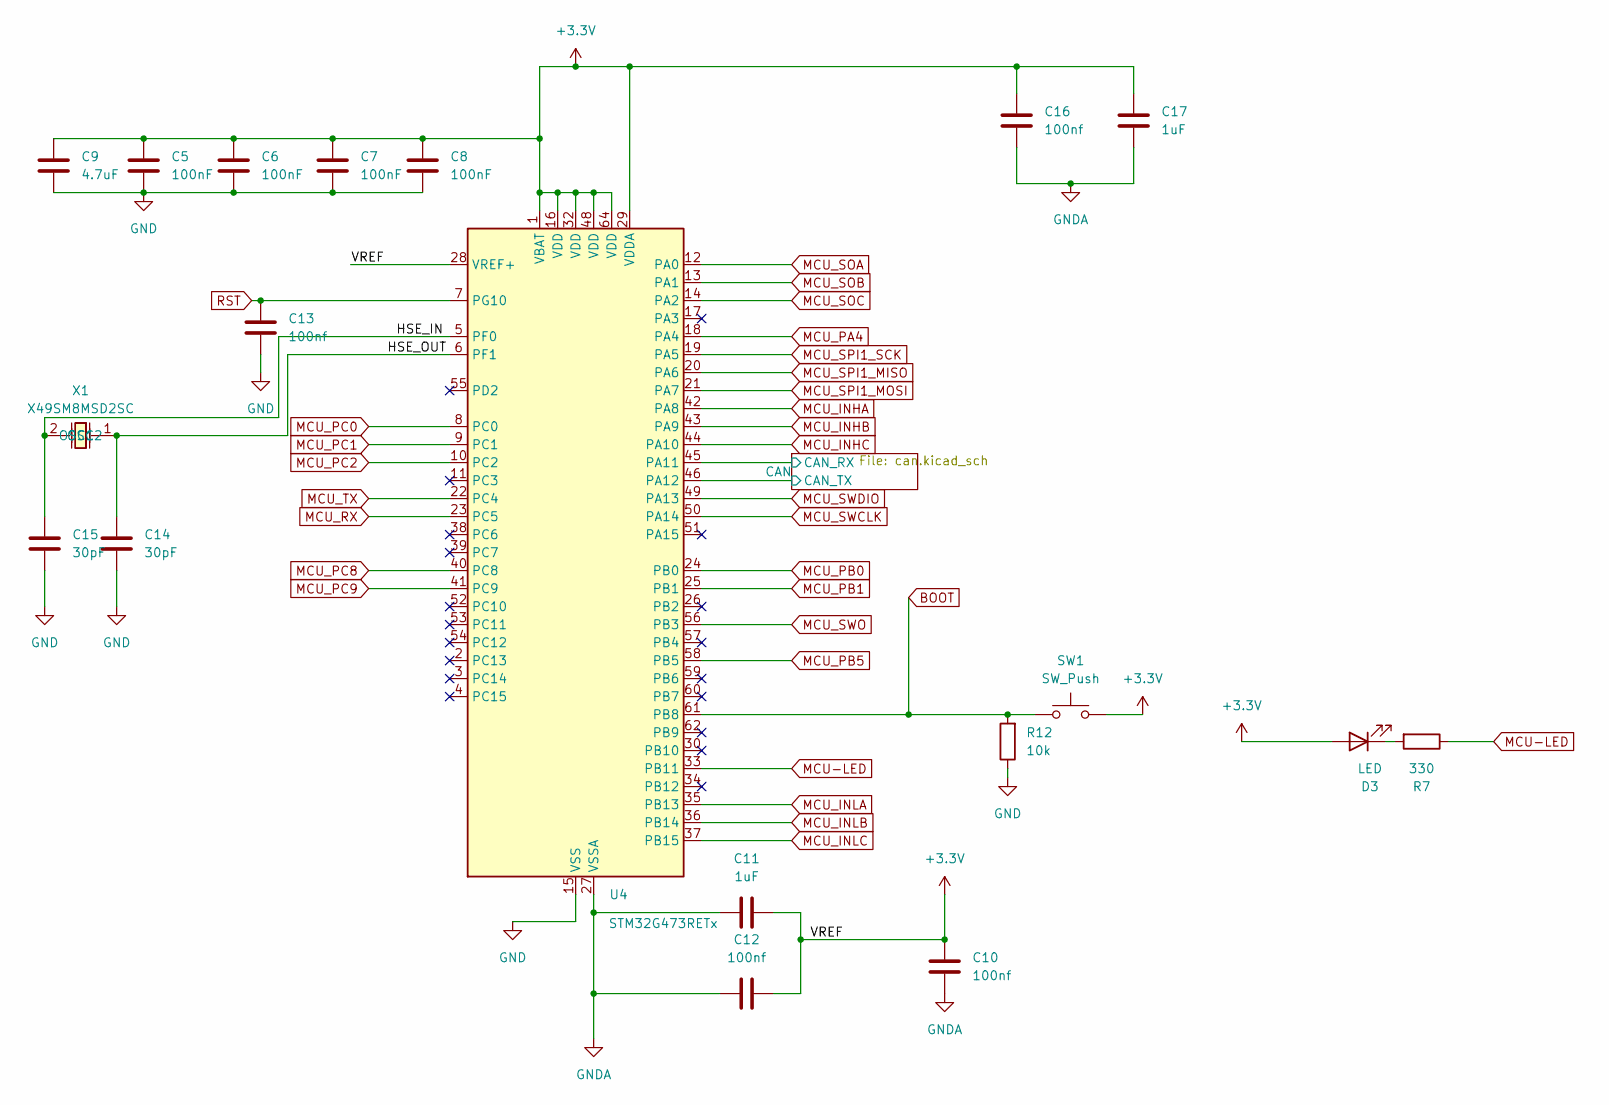
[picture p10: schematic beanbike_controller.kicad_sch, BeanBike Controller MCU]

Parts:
C5, C6, C7, C8: 100nF; C_0402_1005Metric; LCSC C1525
C9: 4.7uF; C_0402_1005Metric; LCSC C1569
C10, C12, C13, C16: 100nf; C_0402_1005Metric; LCSC C1525
C11, C17: 1uF; C_0402_1005Metric; LCSC C52923
C14, C15: 30pF; C_0402_1005Metric; LCSC C1570
D3: LED; LED_0805_2012Metric; LCSC C2297
R7: 330; R_0805_2012Metric; LCSC C17630
R12: 10k; R_0805_2012Metric; LCSC C17414
SW1: SW_Push; SW-SMD_L3.9-W3.0-P4.45; LCSC C720477
U4: STM32G473RETx; LQFP-64_10x10mm_P0.5mm; LCSC C730120
X1: X49SM8MSD2SC; CRYSTAL-SMD_L11.5-W4.8-LS12.7; LCSC Part C12674

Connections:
+3.3V: C5.2, C6.2, C7.2, C8.2, C9.1, C10.1, C11.2, C12.2, C16.1, C17.1, D3.2 (A), SW1.2, U4.1 (VBAT), U4.16 (VDD), U4.28 (VREF+), U4.29 (VDDA), U4.32 (VDD), U4.48 (VDD), U4.64 (VDD); also elsewhere on the board
/MCU/CAN/CAN_RX: U4.45 (PA11); also elsewhere on the board
/MCU/CAN/CAN_TX: U4.46 (PA12); also elsewhere on the board
/MCU/HSE_IN: C15.1, U4.5 (PF0), X1.2 (OSC2)
/MCU/HSE_OUT: C14.1, U4.6 (PF1), X1.1 (OSC1)
BOOT: R12.2, SW1.1, U4.61 (PB8); also elsewhere on the board
BRAKE_GND: C5.1, C6.1, C7.1, C8.1, C9.2, C13.2, C14.2, C15.2, R12.1, U4.15 (VSS), U4.31 (VSS), U4.47 (VSS), U4.63 (VSS); also elsewhere on the board
BRAKE_SIGNAL: U4.58 (PB5); also elsewhere on the board
GNDA: C10.2, C11.1, C12.1, C16.2, C17.2, U4.27 (VSSA)
MCU-LED: R7.1, U4.33 (PB11)
MCU_INHA: U4.42 (PA8); also elsewhere on the board
MCU_INHB: U4.43 (PA9); also elsewhere on the board
MCU_INHC: U4.44 (PA10); also elsewhere on the board
MCU_INLA: U4.35 (PB13); also elsewhere on the board
MCU_INLB: U4.36 (PB14); also elsewhere on the board
MCU_INLC: U4.37 (PB15); also elsewhere on the board
MCU_PA4: U4.18 (PA4); also elsewhere on the board
MCU_PB0: U4.24 (PB0); also elsewhere on the board
MCU_PB1: U4.25 (PB1); also elsewhere on the board
MCU_PC0: U4.8 (PC0); also elsewhere on the board
MCU_PC1: U4.9 (PC1); also elsewhere on the board
MCU_PC2: U4.10 (PC2); also elsewhere on the board
MCU_PC8: U4.40 (PC8); also elsewhere on the board
MCU_PC9: U4.41 (PC9); also elsewhere on the board
MCU_RX: U4.23 (PC5)
MCU_SOA: U4.12 (PA0); also elsewhere on the board
MCU_SOB: U4.13 (PA1); also elsewhere on the board
MCU_SOC: U4.14 (PA2); also elsewhere on the board
MCU_SPI1_MISO: U4.20 (PA6); also elsewhere on the board
MCU_SPI1_MOSI: U4.21 (PA7); also elsewhere on the board
MCU_SPI1_SCK: U4.19 (PA5); also elsewhere on the board
MCU_SWCLK: U4.50 (PA14); also elsewhere on the board
MCU_SWDIO: U4.49 (PA13); also elsewhere on the board
MCU_SWO: U4.56 (PB3); also elsewhere on the board
MCU_TX: U4.22 (PC4)
unnamed: D3.1 (K), R7.2
RST: C13.1, U4.7 (PG10); also elsewhere on the board

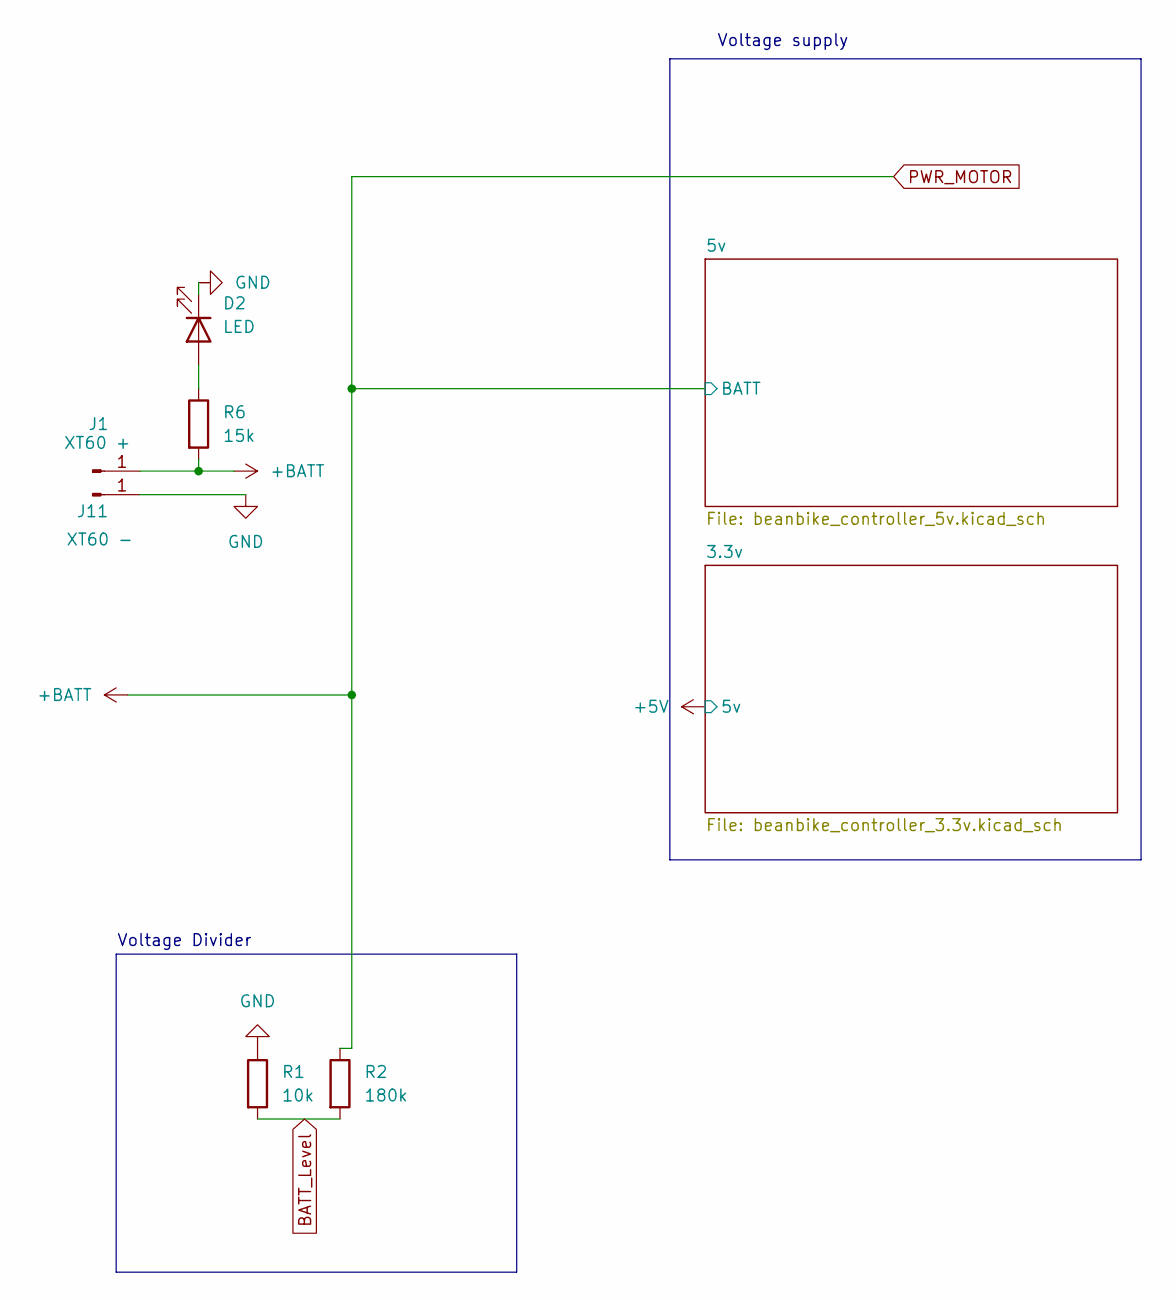
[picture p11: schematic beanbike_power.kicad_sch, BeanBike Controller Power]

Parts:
D2: LED; LED_0603_1608Metric; LCSC C2286
J1: XT60 +; MountingHole_3.2mm_M3_Pad_Via
J11: XT60 -; MountingHole_3.2mm_M3_Pad_Via
R1: 10k; R_0805_2012Metric; LCSC C17414
R2: 180k; R_0805_2012Metric; LCSC C17501
R6: 15k; R_0805_2012Metric; LCSC C17475

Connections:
BATT_Level: R1.2, R2.2
BRAKE_GND: D2.1 (K), J11.1, R1.1; also elsewhere on the board
unnamed: D2.2 (A), R6.1
PWR_MOTOR: J1.1, R2.1, R6.2; also elsewhere on the board

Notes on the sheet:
Voltage Divider
Voltage supply

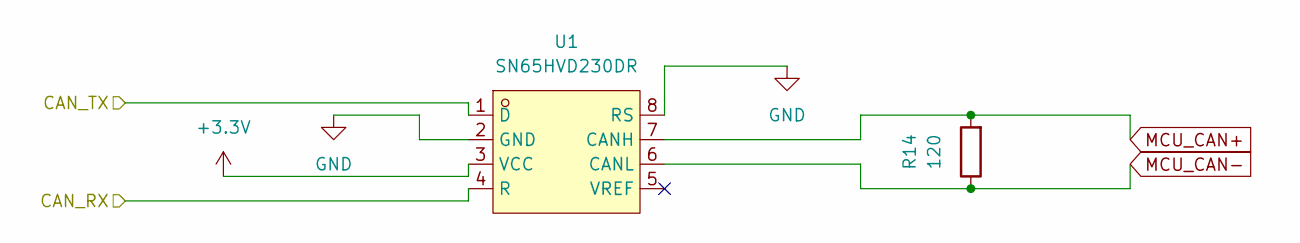
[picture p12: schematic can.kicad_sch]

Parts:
R14: 120; R_0805_2012Metric; LCSC C17437
U1: SN65HVD230DR; SOIC-8_L4.9-W3.9-P1.27-LS6.0-BL; LCSC Part C12084

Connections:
+3.3V: U1.3 (VCC); also elsewhere on the board
/MCU/CAN/CAN_RX: U1.4 (R); also elsewhere on the board
/MCU/CAN/CAN_TX: U1.1 (D); also elsewhere on the board
BRAKE_GND: U1.2 (GND), U1.8 (RS); also elsewhere on the board
MCU_CAN+: R14.2, U1.7 (CANH); also elsewhere on the board
MCU_CAN-: R14.1, U1.6 (CANL); also elsewhere on the board

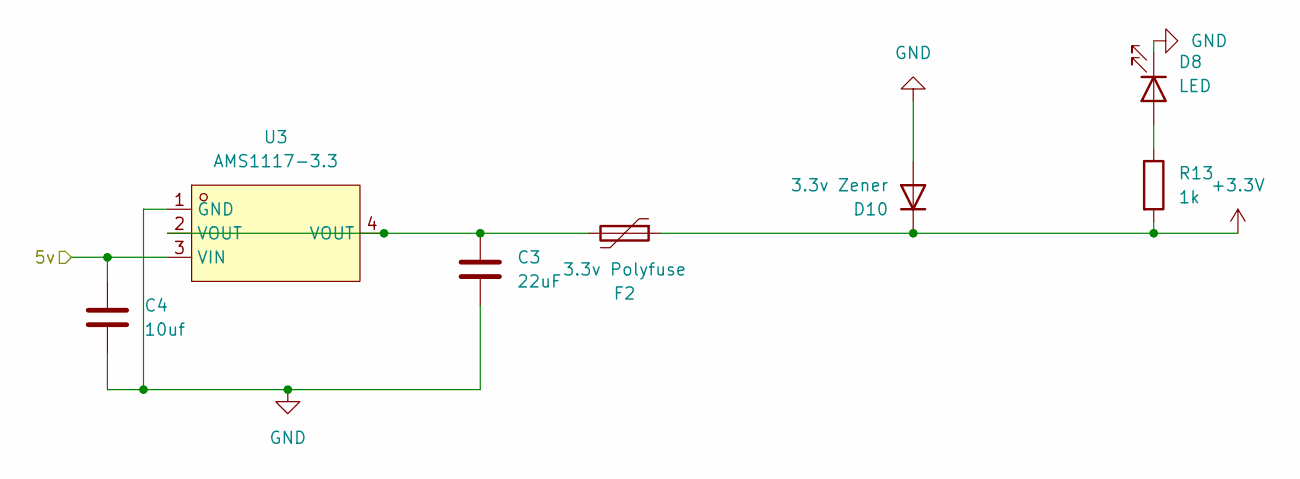
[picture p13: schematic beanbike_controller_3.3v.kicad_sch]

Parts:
C3: 22uF; C_0603_1608Metric; LCSC C59461
C4: 10uf; C_0402_1005Metric; LCSC C15525
D8: LED; LED_0603_1608Metric; LCSC C2290
D10: 3.3v Zener; D_SMA; LCSC C19077475
F2: 3.3v Polyfuse; FUSE_MF_R065_2_BRN
R13: 1k; R_0805_2012Metric; LCSC C17513
U3: AMS1117-3.3; SOT-223-3_L6.5-W3.4-P2.30-LS7.0-BR; LCSC Part C6186

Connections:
+3.3V: D10.1 (K), F2.1, R13.2; also elsewhere on the board
BRAKE_GND: C3.2, C4.2, D8.1 (K), D10.2 (A), U3.1 (GND); also elsewhere on the board
DISPLAY_5V: C4.1, U3.3 (VIN); also elsewhere on the board
unnamed: C3.1, F2.2, U3.2 (VOUT), U3.4 (VOUT)
unnamed: D8.2 (A), R13.1

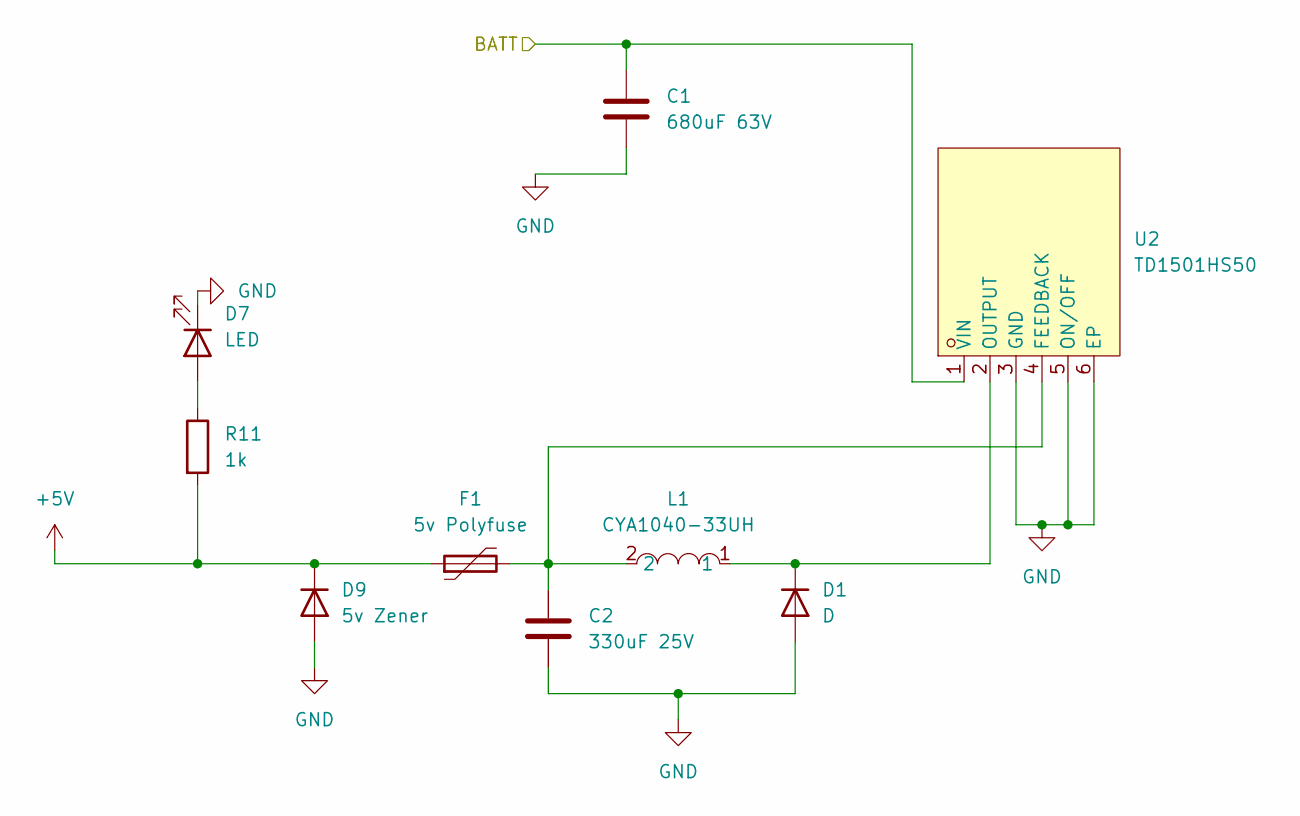
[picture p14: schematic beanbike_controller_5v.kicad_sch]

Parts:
C1: 680uF 63V; CP_Radial_D12.5mm_P5.00mm
C2: 330uF 25V; CP_Radial_D8.0mm_P3.50mm
D1: D; D_SOD-123F; LCSC C64898
D7: LED; LED_0603_1608Metric; LCSC C2296
D9: 5v Zener; D_SMA; LCSC C19077477
F1: 5v Polyfuse; FUS_RKEF300_TYCO_TYC
L1: CYA1040-33UH; IND-SMD_L11.6-W10.1; LCSC Part C6364680
R11: 1k; R_0805_2012Metric; LCSC C17513
U2: TD1501HS50; PG-TO-263-5_L10.2-W8.7-P1.70-LS14.4-BR; LCSC Part C134490

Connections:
BRAKE_GND: C1.2, C2.2, D1.2 (A), D7.1 (K), D9.2 (A), U2.3 (GND), U2.5 (ON/OFF), U2.6 (EP); also elsewhere on the board
DISPLAY_5V: D9.1 (K), F1.1, R11.2; also elsewhere on the board
unnamed: D1.1 (K), L1.1, U2.2 (OUTPUT)
unnamed: D7.2 (A), R11.1
unnamed: C2.1, F1.2, L1.2, U2.4 (FEEDBACK)
PWR_MOTOR: C1.1, U2.1 (VIN); also elsewhere on the board

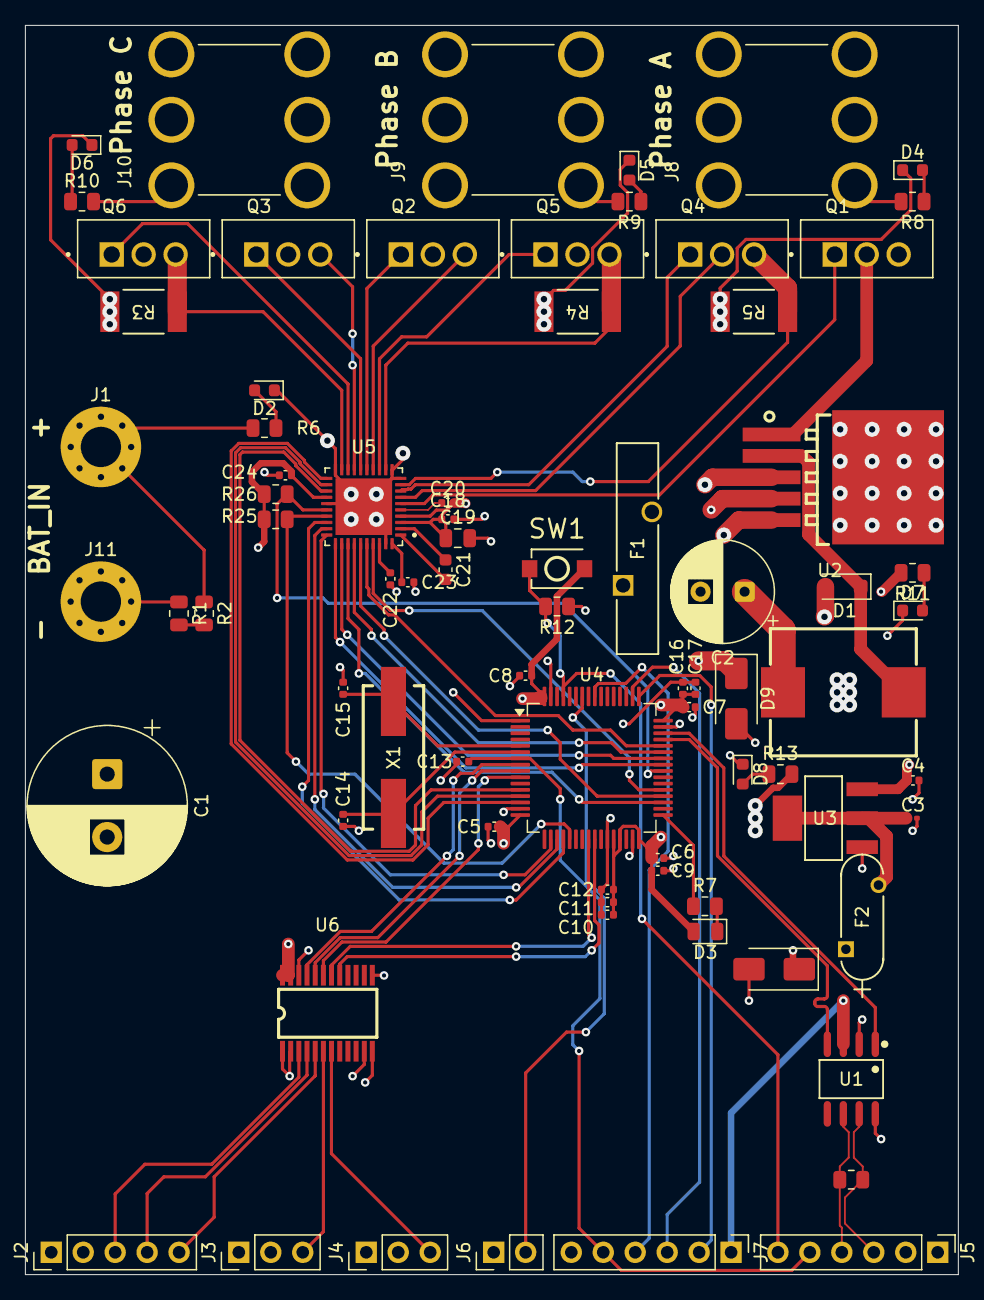
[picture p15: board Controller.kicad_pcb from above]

Board: 4 copper layers, 74.1 x 99.3 mm, 78 parts (0 on the bottom side), 71 nets.

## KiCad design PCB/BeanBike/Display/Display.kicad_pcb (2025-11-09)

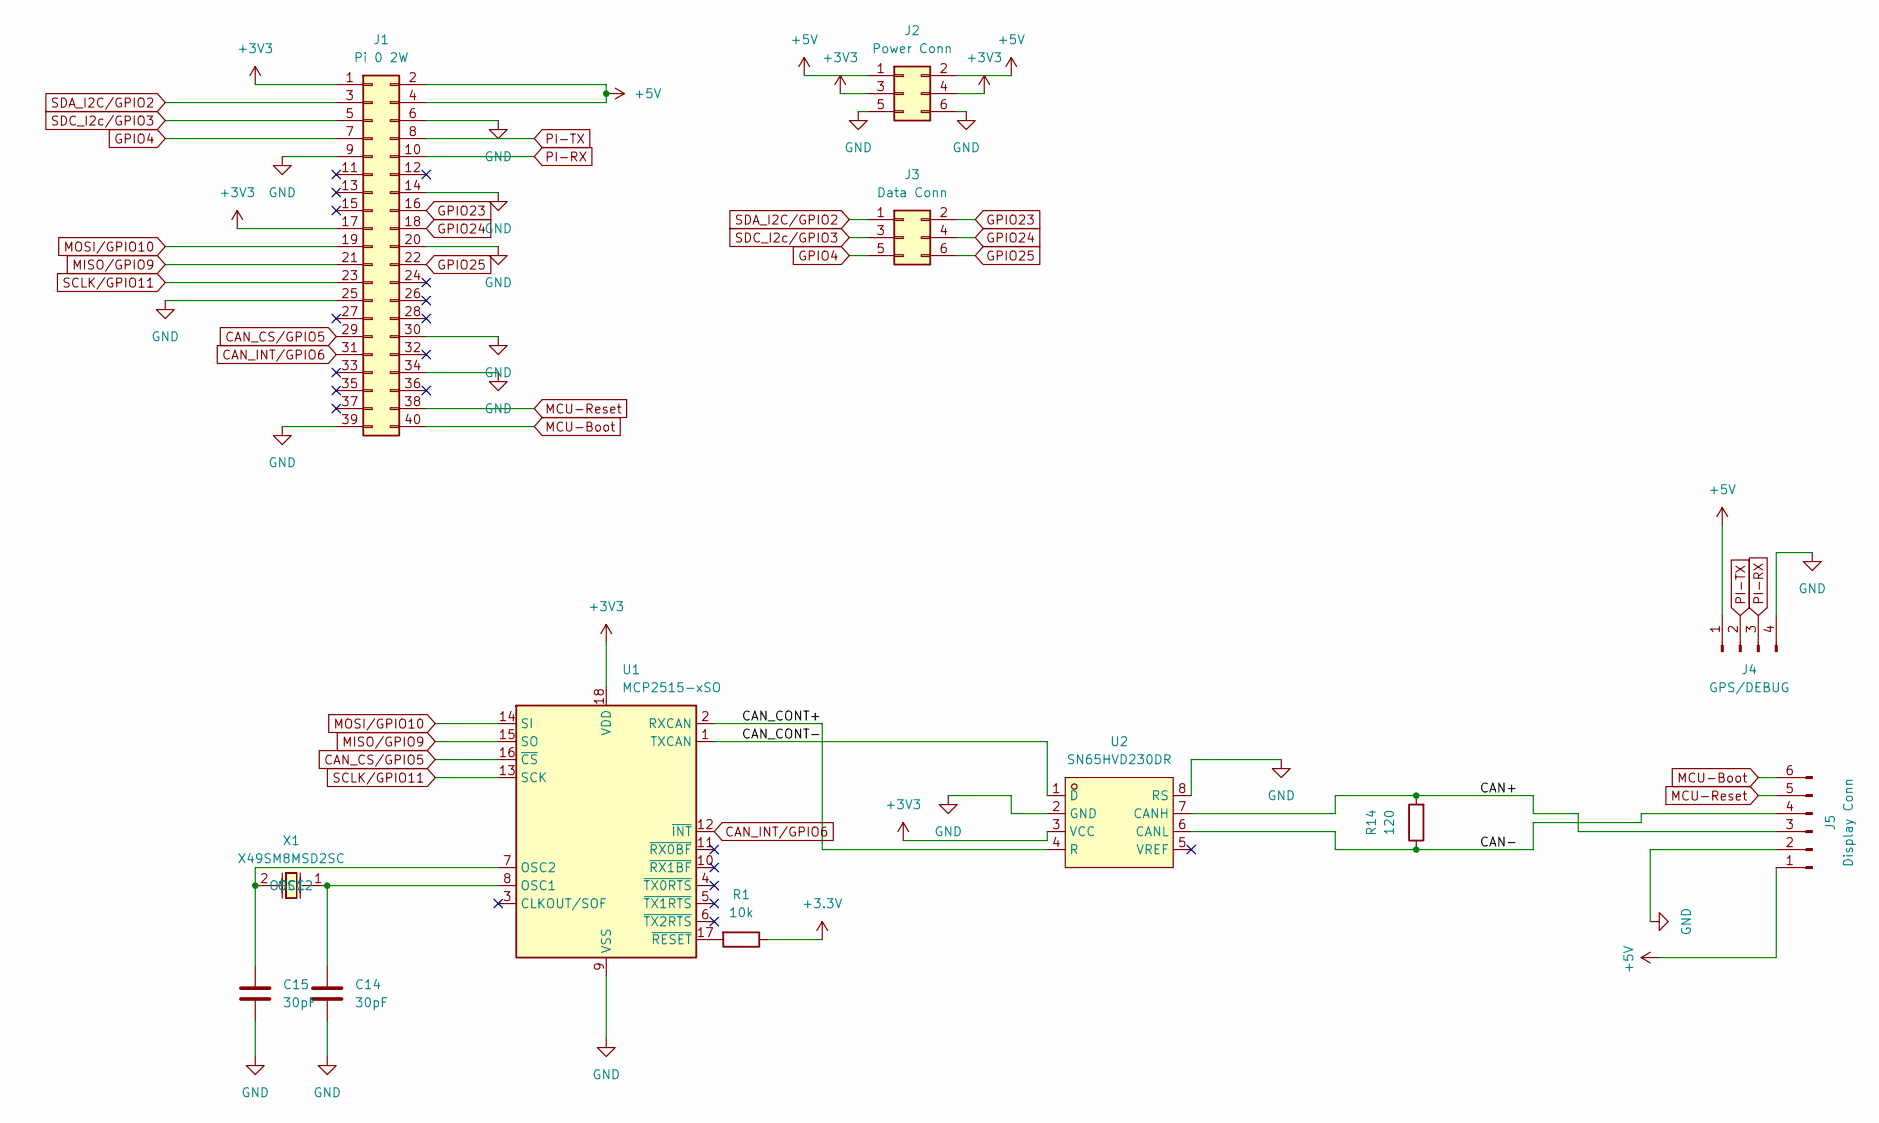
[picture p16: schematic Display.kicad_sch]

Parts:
C14, C15: 30pF; C_0402_1005Metric; LCSC C1570
J1: Pi 0 2W; PinSocket_2x20_P2.54mm_Vertical
J2: Power Conn; PinHeader_2x03_P2.54mm_Vertical
J3: Data Conn; PinHeader_2x03_P2.54mm_Vertical
J4: GPS/DEBUG; PinHeader_1x04_P2.54mm_Vertical
J5: Display Conn; PinHeader_1x06_P2.54mm_Vertical
R1: 10k; R_0805_2012Metric; LCSC C17414
R14: 120; R_0805_2012Metric; LCSC C17437
U1: MCP2515-xSO; SOIC-18W_7.5x11.6mm_P1.27mm; LCSC C15193
U2: SN65HVD230DR; SOIC-8_L4.9-W3.9-P1.27-LS6.0-BL; LCSC Part C12084
X1: X49SM8MSD2SC; CRYSTAL-SMD_L11.5-W4.8-LS12.7; LCSC Part C12674

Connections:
+3.3V: R1.1
+3V3: J1.1, J1.17, J2.3, J2.4, U1.18 (VDD), U2.3 (VCC)
+5V: J1.2, J1.4, J2.1, J2.2, J4.1, J5.1
/CAN+: J5.3, R14.2, U2.7 (CANH)
/CAN-: J5.4, R14.1, U2.6 (CANL)
/CAN_CONT+: U1.2 (RXCAN), U2.4 (R)
/CAN_CONT-: U1.1 (TXCAN), U2.1 (D)
CAN_CS/GPIO5: J1.29, U1.16 (~CS)
CAN_INT/GPIO6: J1.31, U1.12 (~INT)
GND: C14.2, C15.2, J1.6, J1.9, J1.14, J1.20, J1.25, J1.30, J1.34, J1.39, J2.5, J2.6, J4.4, J5.2, U1.9 (VSS), U2.2 (GND), U2.8 (RS)
GPIO4: J1.7, J3.5
GPIO23: J1.16, J3.2
GPIO24: J1.18, J3.4
GPIO25: J1.22, J3.6
MCU-Boot: J1.40, J5.6
MCU-Reset: J1.38, J5.5
MISO/GPIO9: J1.21, U1.15 (SO)
MOSI/GPIO10: J1.19, U1.14 (SI)
unnamed: C14.1, U1.8 (OSC1), X1.1 (OSC1)
unnamed: C15.1, U1.7 (OSC2), X1.2 (OSC2)
unnamed: R1.2, U1.17 (~RESET)
PI-RX: J1.10, J4.3
PI-TX: J1.8, J4.2
SCLK/GPIO11: J1.23, U1.13 (SCK)
SDA_I2C/GPIO2: J1.3, J3.1
SDC_I2c/GPIO3: J1.5, J3.3

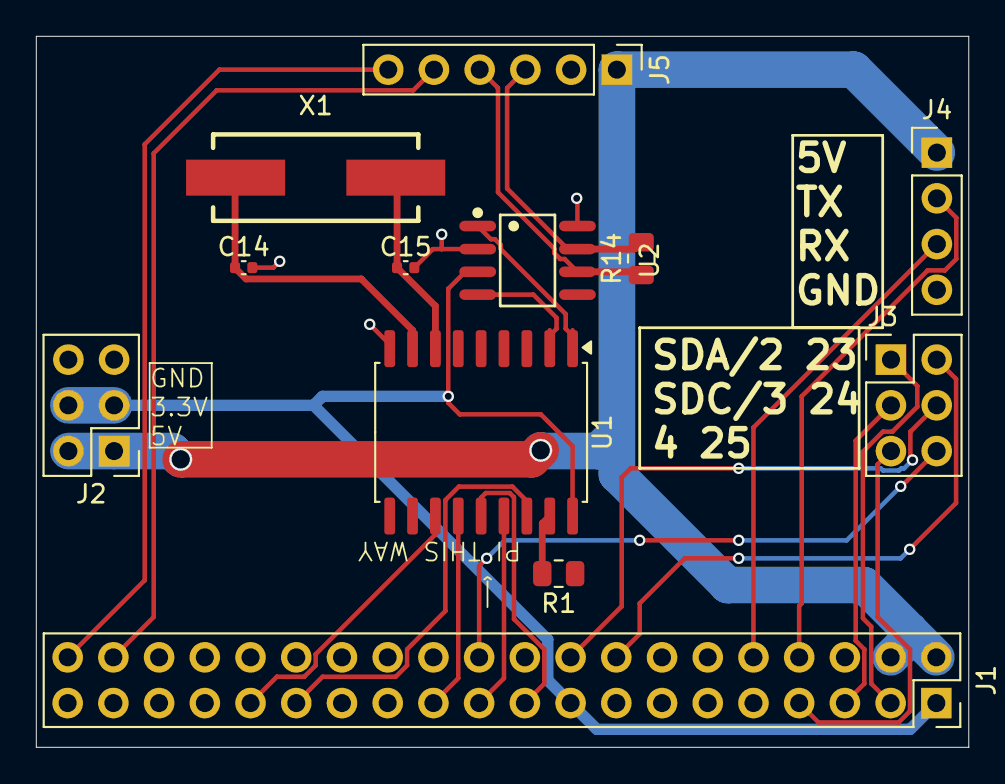
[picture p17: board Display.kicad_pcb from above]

Board: 2 copper layers, 51.8 x 39.5 mm, 12 parts (0 on the bottom side), 25 nets.

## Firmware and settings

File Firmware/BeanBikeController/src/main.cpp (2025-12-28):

#include <Arduino.h>
#include <SPI.h>

// DRV8353S SPI + control pins
const int DRV_CS_PIN     = PA4;   // SPI CS
const int DRV_ENABLE_PIN = PC9;   // nSLEEP / ENABLE
const int DRV_FAULT_PIN  = PC8;   // nFAULT (active low)

// Motor driver pins (6-PWM)
const int PWM_PIN_AH = PA8;       // Phase A High
const int PWM_PIN_AL = PB13;      // Phase A Low
const int PWM_PIN_BH = PA9;       // Phase B High
const int PWM_PIN_BL = PB14;      // Phase B Low
const int PWM_PIN_CH = PA10;      // Phase C High
const int PWM_PIN_CL = PB15;      // Phase C Low

// Current sense inputs (not used here, keep as inputs)
const int SOA_PIN = PA0;
const int SOB_PIN = PA1;
const int SOC_PIN = PA2;

// Status LED
const int LED_PIN = PB5;

// SPI pins (STM32 default SPI1)
const int SPI_MOSI = PA7;  // SPI1_MOSI
const int SPI_MISO = PA6;  // SPI1_MISO
const int SPI_SCK  = PA5;  // SPI1_SCK

// DRV8353S register addresses
#define DRV8353_FAULT_STATUS_1 0x00
#define DRV8353_FAULT_STATUS_2 0x01
#define DRV8353_DRIVER_CONTROL 0x02
#define DRV8353_GATE_DRIVE_HS  0x03
#define DRV8353_GATE_DRIVE_LS  0x04
#define DRV8353_OCP_CONTROL    0x05
#define DRV8353_CSA_CONTROL    0x06

// SPI settings for DRV8353
// DRV8353 datasheet: Mode 1 (CPOL=0, CPHA=1), max 10 MHz
// Start VERY slow for debugging - 100kHz
SPISettings drvSPISettings(100000, MSBFIRST, SPI_MODE1);

// ========== DRV8353 SPI Functions ==========

/**
 * Manual bit-bang SPI test to verify hardware wiring
 * This bypasses the SPI hardware to test physical connections
 */
void manualSPITest() {
  Serial.println("\n========== Manual Bit-Bang SPI Test ==========");
  Serial.println("Testing hardware by manually toggling pins...");
  
  // Set pins to manual control
  pinMode(SPI_SCK, OUTPUT);
  pinMode(SPI_MOSI, OUTPUT);
  pinMode(SPI_MISO, INPUT);
  pinMode(DRV_CS_PIN, OUTPUT);
  
  digitalWrite(DRV_CS_PIN, HIGH);
  digitalWrite(SPI_SCK, LOW);  // CPOL=0
  digitalWrite(SPI_MOSI, LOW);
  delay(10);
  
  Serial.print("  Initial MISO state: ");
  Serial.println(digitalRead(SPI_MISO) ? "HIGH" : "LOW");
  
  // Send a byte manually (0xAA = 10101010)
  digitalWrite(DRV_CS_PIN, LOW);
  delayMicroseconds(10);
  
  uint8_t testByte = 0xAA;
  uint8_t received = 0;
  
  Serial.println("  Sending 0xAA (10101010) bit by bit:");
  
  for (int i = 7; i >= 0; i--) {
    // Set MOSI
    bool bitOut = (testByte >> i) & 0x01;
    digitalWrite(SPI_MOSI, bitOut);
    delayMicroseconds(10);
    
    // Rising edge (Mode 1: CPHA=1, data captured on rising edge)
    digitalWrite(SPI_SCK, HIGH);
    delayMicroseconds(10);
    
    // Read MISO
    bool bitIn = digitalRead(SPI_MISO);
    received = (received << 1) | bitIn;
    
    Serial.print("    Bit ");
    Serial.print(7 - i);
    Serial.print(": MOSI=");
    Serial.print(bitOut);
    Serial.print(", MISO=");
    Serial.println(bitIn);
    
    // Falling edge
    digitalWrite(SPI_SCK, LOW);
    delayMicroseconds(10);
  }
  
  digitalWrite(DRV_CS_PIN, HIGH);
  
  Serial.print("  Sent: 0x");
  Serial.print(testByte, HEX);
  Serial.print(", Received: 0x");
  Serial.println(received, HEX);
  
  if (received == 0xFF) {
    Serial.println("  ⚠️  MISO is stuck HIGH - not responding to clock!");
    Serial.println("  This confirms hardware issue:");
    Serial.println("    - DRV8353 SDO pin not connected to PA6, OR");
    Serial.println("    - DRV8353 PVDD not powered, OR");
    Serial.println("    - Wrong DRV8353 variant (M series has no SPI)");
  } else if (received == 0x00) {
    Serial.println("  ⚠️  MISO is stuck LOW - short to ground?");
  } else {
    Serial.println("  ✓ MISO is responding! SPI hardware should work.");
  }
  
  Serial.println("==============================================\n");
  
  // Re-initialize SPI hardware
  SPI.begin();
}

/**
 * Test different SPI modes to find which works
 */
void testSPIModes() {
  Serial.println("\n========== Testing SPI Modes ==========");
  
  const uint8_t modes[] = {SPI_MODE0, SPI_MODE1, SPI_MODE2, SPI_MODE3};
  const char* modeNames[] = {"MODE0 (CPOL=0,CPHA=0)", "MODE1 (CPOL=0,CPHA=1)", 
                             "MODE2 (CPOL=1,CPHA=0)", "MODE3 (CPOL=1,CPHA=1)"};
  
  for (int i = 0; i < 4; i++) {
    Serial.print("\nTesting SPI ");
    Serial.println(modeNames[i]);
    
    SPISettings testSettings(100000, MSBFIRST, modes[i]);  // 100kHz for testing
    SPI.beginTransaction(testSettings);
    
    // Try to read Fault Status 1 register
    uint16_t command = (1 << 15) | ((0x00 & 0x0F) << 11);  // Read register 0x00
    
    digitalWrite(DRV_CS_PIN, LOW);
    delayMicroseconds(10);
    uint16_t response = SPI.transfer16(command);
    delayMicroseconds(10);
    digitalWrite(DRV_CS_PIN, HIGH);
    
    SPI.endTransaction();
    
    Serial.print("  Command: 0x");
    Serial.print(command, HEX);
    Serial.print(" | Response: 0x");
    Serial.print(response, HEX);
    
    if (response != 0xFFFF && response != 0x0000) {
      Serial.println(" ← VALID RESPONSE!");
    } else {
      Serial.println(" (no response)");
    }
    
    delay(10);
  }
  
  Serial.println("\n=======================================\n");
}

/**
 * Read a 16-bit register from DRV8353
 * Frame format: [R/W(1)][A3-A0(4)][D10-D0(11)]
 * R/W = 1 for read
 * 
 * DRV8353 SPI Timing (from datasheet):
 * - CS setup time: min 50ns
 * - CS hold time: min 50ns  
 * - Clock frequency: max 10MHz
 * - Data valid after falling edge of SCK
 */
uint16_t drv8353_readRegister(uint8_t address) {
  // Construct read command: R/W=1, address in bits [14:11]
  uint16_t command = (1 << 15) | ((address & 0x0F) << 11);
  
  // CS setup time (datasheet: min 50ns, using 2us to be safe)
  digitalWrite(DRV_CS_PIN, LOW);
  delayMicroseconds(2);
  
  // Send command and receive response
  // Try sending as two bytes to check byte order
  uint8_t cmdHigh = (command >> 8) & 0xFF;
  uint8_t cmdLow = command & 0xFF;
  
  uint8_t respHigh = SPI.transfer(cmdHigh);
  uint8_t respLow = SPI.transfer(cmdLow);
  
  uint16_t response = (respHigh << 8) | respLow;
  
  // CS hold time (datasheet: min 50ns, using 2us to be safe)
  delayMicroseconds(2);
  digitalWrite(DRV_CS_PIN, HIGH);
  delayMicroseconds(5);  // Inter-transaction delay
  
  // Extract 11-bit data (bits 10:0)
  uint16_t data = response & 0x07FF;
  
  Serial.print("  [SPI READ] Addr: 0x");
  Serial.print(address, HEX);
  Serial.print(" | Command: 0x");
  Serial.print(command, HEX);
  Serial.print(" | Response: 0x");
  Serial.print(response, HEX);
  Serial.print(" | Data: 0x");
  Serial.println(data, HEX);
  
  return data;
}

/**
 * Write a 16-bit register to DRV8353
 * Frame format: [R/W(1)][A3-A0(4)][D10-D0(11)]
 * R/W = 0 for write
 */
void drv8353_writeRegister(uint8_t address, uint16_t data) {
  // Construct write command: R/W=0, address in bits [14:11], data in bits [10:0]
  uint16_t command = (0 << 15) | ((address & 0x0F) << 11) | (data & 0x07FF);
  
  // CS setup time
  digitalWrite(DRV_CS_PIN, LOW);
  delayMicroseconds(2);
  
  // Send as two bytes
  uint8_t cmdHigh = (command >> 8) & 0xFF;
  uint8_t cmdLow = command & 0xFF;
  
  uint8_t respHigh = SPI.transfer(cmdHigh);
  uint8_t respLow = SPI.transfer(cmdLow);
  
  uint16_t response = (respHigh << 8) | respLow;
  
  // CS hold time
  delayMicroseconds(2);
  digitalWrite(DRV_CS_PIN, HIGH);
  delayMicroseconds(5);  // Inter-transaction delay
  
  Serial.print("  [SPI WRITE] Addr: 0x");
  Serial.print(address, HEX);
  Serial.print(" | Data: 0x");
  Serial.print(data, HEX);
  Serial.print(" | Command: 0x");
  Serial.print(command, HEX);
  Serial.print(" | Response: 0x");
  Serial.println(response, HEX);
}

/**
 * Initialize DRV8353
 */
bool drv8353_init() {
  Serial.println("\n========== DRV8353 Initialization ==========");
  
  // Step 1: Enable the driver (bring out of sleep) - may already be enabled
  bool alreadyEnabled = digitalRead(DRV_ENABLE_PIN);
  if (!alreadyEnabled) {
    Serial.println("Step 1: Enabling DRV8353 (nSLEEP HIGH)...");
    digitalWrite(DRV_ENABLE_PIN, HIGH);
    delay(10);  // Wait for power-up (datasheet: typ 1ms)
  } else {
    Serial.println("Step 1: DRV8353 already enabled, skipping...");
  }
  
  // Step 2: Check fault pin
  bool faultState = digitalRead(DRV_FAULT_PIN);
  Serial.print("Step 2: Fault pin state: ");
  Serial.println(faultState ? "HIGH (No Fault)" : "LOW (FAULT DETECTED!)");
  
  // Step 3: Read fault status registers
  Serial.println("\nStep 3: Reading Fault Status Registers...");
  uint16_t fault1 = drv8353_readRegister(DRV8353_FAULT_STATUS_1);
  uint16_t fault2 = drv8353_readRegister(DRV8353_FAULT_STATUS_2);
  
  Serial.println("\n--- Fault Status 1 Breakdown (0x00) ---");
  Serial.print("  VDS_LC:  "); Serial.println((fault1 >> 0) & 0x01 ? "FAULT" : "OK");
  Serial.print("  VDS_HC:  "); Serial.println((fault1 >> 1) & 0x01 ? "FAULT" : "OK");
  Serial.print("  VDS_LB:  "); Serial.println((fault1 >> 2) & 0x01 ? "FAULT" : "OK");
  Serial.print("  VDS_HB:  "); Serial.println((fault1 >> 3) & 0x01 ? "FAULT" : "OK");
  Serial.print("  VDS_LA:  "); Serial.println((fault1 >> 4) & 0x01 ? "FAULT" : "OK");
  Serial.print("  VDS_HA:  "); Serial.println((fault1 >> 5) & 0x01 ? "FAULT" : "OK");
  Serial.print("  OTSD:    "); Serial.println((fault1 >> 6) & 0x01 ? "FAULT" : "OK");
  Serial.print("  UVLO:    "); Serial.println((fault1 >> 7) & 0x01 ? "FAULT" : "OK");
  Serial.print("  GDF:     "); Serial.println((fault1 >> 8) & 0x01 ? "FAULT" : "OK");
  Serial.print("  VDS_OCP: "); Serial.println((fault1 >> 9) & 0x01 ? "FAULT" : "OK");
  Serial.print("  FAULT:   "); Serial.println((fault1 >> 10) & 0x01 ? "YES" : "NO");
  
  Serial.println("\n--- Fault Status 2 Breakdown (0x01) ---");
  Serial.print("  VGS_LC:  "); Serial.println((fault2 >> 0) & 0x01 ? "FAULT" : "OK");
  Serial.print("  VGS_HC:  "); Serial.println((fault2 >> 1) & 0x01 ? "FAULT" : "OK");
  Serial.print("  VGS_LB:  "); Serial.println((fault2 >> 2) & 0x01 ? "FAULT" : "OK");
  Serial.print("  VGS_HB:  "); Serial.println((fault2 >> 3) & 0x01 ? "FAULT" : "OK");
  Serial.print("  VGS_LA:  "); Serial.println((fault2 >> 4) & 0x01 ? "FAULT" : "OK");
  Serial.print("  VGS_HA:  "); Serial.println((fault2 >> 5) & 0x01 ? "FAULT" : "OK");
  Serial.print("  CPUV:    "); Serial.println((fault2 >> 6) & 0x01 ? "FAULT" : "OK");
  Serial.print("  OTW:     "); Serial.println((fault2 >> 7) & 0x01 ? "WARNING" : "OK");
  Serial.print("  SC_OC:   "); Serial.println((fault2 >> 8) & 0x01 ? "FAULT" : "OK");
  Serial.print("  SB_OC:   "); Serial.println((fault2 >> 9) & 0x01 ? "FAULT" : "OK");
  Serial.print("  SA_OC:   "); Serial.println((fault2 >> 10) & 0x01 ? "FAULT" : "OK");
  
  // Step 4: Configure driver control register
  Serial.println("\nStep 4: Configuring Driver Control Register (0x02)...");
  // Default: 6-PWM mode, no override
  uint16_t driverCtrl = 0x0000;  // Start with defaults
  // Bit 8: CLR_FLT = 0 (don't clear faults yet)
  // Bit 7: BRAKE = 0 (no brake)
  // Bit 6: COAST = 0 (no coast)
  // Bit 5-4: PWM_MODE = 00 (6x PWM mode)
  // Bit 3: 1PWM_COM = 0
  // Bit 2: 1PWM_DIR = 0
  // Bit 1-0: OCP_ACT = 00 (shutdown on OCP)
  drv8353_writeRegister(DRV8353_DRIVER_CONTROL, driverCtrl);
  
  // Verify write
  uint16_t driverCtrlRead = drv8353_readRegister(DRV8353_DRIVER_CONTROL);
  Serial.print("  Driver Control readback: 0x");
  Serial.println(driverCtrlRead, HEX);
  
  // Step 5: Configure gate drive settings
  Serial.println("\nStep 5: Configuring Gate Drive High-Side (0x03)...");
  // IDRIVEP_HS = IDRIVEN_HS = 1000mA (bits [7:4] and [3:0] = 0101 = 5)
  // LOCK bits [10:8] = 110 to unlock
  uint16_t gateHS = (0x06 << 8) | (0x05 << 4) | (0x05 << 0);
  drv8353_writeRegister(DRV8353_GATE_DRIVE_HS, gateHS);
  uint16_t gateHSRead = drv8353_readRegister(DRV8353_GATE_DRIVE_HS);
  Serial.print("  Gate Drive HS readback: 0x");
  Serial.println(gateHSRead, HEX);
  
  Serial.println("\nStep 6: Configuring Gate Drive Low-Side (0x04)...");
  // Similar settings for low side
  uint16_t gateLS = (0x06 << 8) | (0x05 << 4) | (0x05 << 0);
  drv8353_writeRegister(DRV8353_GATE_DRIVE_LS, gateLS);
  uint16_t gateLSRead = drv8353_readRegister(DRV8353_GATE_DRIVE_LS);
  Serial.print("  Gate Drive LS readback: 0x");
  Serial.println(gateLSRead, HEX);
  
  // Step 6: Configure OCP (overcurrent protection)
  Serial.println("\nStep 7: Configuring OCP Control (0x05)...");
  // VDS_LVL = 0.06V (bits [3:0] = 0001), everything else default
  uint16_t ocpCtrl = 0x0001;
  drv8353_writeRegister(DRV8353_OCP_CONTROL, ocpCtrl);
  uint16_t ocpCtrlRead = drv8353_readRegister(DRV8353_OCP_CONTROL);
  Serial.print("  OCP Control readback: 0x");
  Serial.println(ocpCtrlRead, HEX);
  
  // Step 7: Configure CSA (current sense amplifier)
  Serial.println("\nStep 8: Configuring CSA Control (0x06)...");
  // CSA_GAIN = 10V/V (bits [7:6] = 01), everything else default
  uint16_t csaCtrl = (0x01 << 6);
  drv8353_writeRegister(DRV8353_CSA_CONTROL, csaCtrl);
  uint16_t csaCtrlRead = drv8353_readRegister(DRV8353_CSA_CONTROL);
  Serial.print("  CSA Control readback: 0x");
  Serial.println(csaCtrlRead, HEX);
  
  Serial.println("\n========== DRV8353 Initialization Complete ==========\n");
  
  // Check if any faults remain
  if ((fault1 & 0x400) || (fault2 & 0x700)) {
    Serial.println("WARNING: Faults detected during initialization!");
    return false;
  }
  
  return true;
}

/**
 * Read and display all registers
 */
void drv8353_readAllRegisters() {
  Serial.println("\n========== DRV8353 Register Dump ==========");
  for (uint8_t addr = 0x00; addr <= 0x06; addr++) {
    uint16_t value = drv8353_readRegister(addr);
    Serial.print("Register 0x");
    Serial.print(addr, HEX);
    Serial.print(": 0x");
    Serial.print(value, HEX);
    Serial.print(" (");
    Serial.print(value, BIN);
    Serial.println(")");
  }
  Serial.println("===========================================\n");
}
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
void loop() {
  // CRITICAL: Stop immediately on driver fault and enter safe mode
  if (digitalRead(DRV_FAULT_PIN) == LOW) {
    // Turn OFF all motor outputs immediately
    digitalWrite(PWM_PIN_AH, LOW);
    digitalWrite(PWM_PIN_AL, LOW);
    digitalWrite(PWM_PIN_BH, LOW);
    digitalWrite(PWM_PIN_BL, LOW);
    digitalWrite(PWM_PIN_CH, LOW);
    digitalWrite(PWM_PIN_CL, LOW);
    
    Serial.println("\n!!! FAULT DETECTED - ENTERING SAFE MODE !!!");
    Serial.println("All motor outputs disabled.");
    Serial.println("Check DRV8353 fault registers for details.");
    
    // Blink LED twice repeatedly to indicate fault
    while (true) {
      // First blink
      digitalWrite(LED_PIN, HIGH);
      delay(200);
      digitalWrite(LED_PIN, LOW);
      delay(200);
      
      // Second blink
      digitalWrite(LED_PIN, HIGH);
      delay(200);
      digitalWrite(LED_PIN, LOW);
      delay(800); // Longer pause before repeating
      
      Serial.println("FAULT - System halted");
    }
  }

  static uint32_t lastStep = 0;
  static int step = 0;
  // Sweep dwell values between 5–50ms so you can spot a torque sweet spot while it runs
  static const uint8_t dwellTable[] = {5, 10, 15, 20, 25, 30, 35, 40, 45, 50};
  static uint8_t dwellIndex = 0;
  static uint32_t dwellMs = dwellTable[0];
  static uint32_t stepsAtCurrentDwell = 0;
  const uint32_t stepsPerDwell = 240;  // Hold each dwell for ~240 commutation steps (~40 electrical revs)

  if (millis() - lastStep >= dwellMs) {
    lastStep = millis();

    // Turn everything OFF first to avoid shoot-through
    digitalWrite(PWM_PIN_AH, LOW);
    digitalWrite(PWM_PIN_AL, LOW);
    digitalWrite(PWM_PIN_BH, LOW);
    digitalWrite(PWM_PIN_BL, LOW);
    digitalWrite(PWM_PIN_CH, LOW);
    digitalWrite(PWM_PIN_CL, LOW);

    switch (step) {
      case 0: // A+ B-
        digitalWrite(PWM_PIN_AH, HIGH);
        digitalWrite(PWM_PIN_BL, HIGH);
        break;
      case 1: // A+ C-
        digitalWrite(PWM_PIN_AH, HIGH);
        digitalWrite(PWM_PIN_CL, HIGH);
        break;
      case 2: // B+ C-
        digitalWrite(PWM_PIN_BH, HIGH);
        digitalWrite(PWM_PIN_CL, HIGH);
        break;
      case 3: // B+ A-
        digitalWrite(PWM_PIN_BH, HIGH);
        digitalWrite(PWM_PIN_AL, HIGH);
        break;
      case 4: // C+ A-
        digitalWrite(PWM_PIN_CH, HIGH);
        digitalWrite(PWM_PIN_AL, HIGH);
        break;
      case 5: // C+ B-
        digitalWrite(PWM_PIN_CH, HIGH);
        digitalWrite(PWM_PIN_BL, HIGH);
        break;
    }

    step = (step + 5) % 6; // advance commutation - REVERSED direction to test phase order

    // Advance dwell timing after a block of commutation steps
    stepsAtCurrentDwell++;
    if (stepsAtCurrentDwell >= stepsPerDwell) {
      stepsAtCurrentDwell = 0;
      dwellIndex = (dwellIndex + 1) % (sizeof(dwellTable) / sizeof(dwellTable[0]));
      dwellMs = dwellTable[dwellIndex];
      Serial.print("[COMM] Switching dwell to ");
      Serial.print(dwellMs);
      Serial.println(" ms");
    }

    // Blink LED each commutation step
    digitalWrite(LED_PIN, !digitalRead(LED_PIN));
  }
}

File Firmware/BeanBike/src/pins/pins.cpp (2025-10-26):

#include <Arduino.h>
#include "pins.h"
#include "DRV8353.h"
#include "motor.h"
// Pin Definitions
const PinDef Pins::BATT_LEVEL = {"BATT_LEVEL", 16, INPUT};
const PinDef Pins::MOTOR_ENABLE = {"MOTOR_ENABLE", 13, OUTPUT};
const PinDef Pins::MOTOR_INHA = {"MOTOR_INHA", 12, OUTPUT};
const PinDef Pins::MOTOR_INLA = {"MOTOR_INLA", 14, OUTPUT};
const PinDef Pins::MOTOR_INHB = {"MOTOR_INHB", 27, OUTPUT};
const PinDef Pins::MOTOR_INLB = {"MOTOR_INLB", 26, OUTPUT};
const PinDef Pins::MOTOR_INHC = {"MOTOR_INHC", 25, OUTPUT};
const PinDef Pins::MOTOR_INLC = {"MOTOR_INLC", 33, OUTPUT};
const PinDef Pins::MOTOR_SOA = {"MOTOR_SOA", 21, INPUT};
const PinDef Pins::MOTOR_SOB = {"MOTOR_SOB", 22, INPUT};
const PinDef Pins::MOTOR_SOC = {"MOTOR_SOC", 17, INPUT};
const PinDef Pins::MOTOR_FAULT = {"MOTOR_FAULT", 15, INPUT};
const PinDef Pins::MOTOR_HALL_A = {"MOTOR_HALL_A", 9, INPUT};
const PinDef Pins::MOTOR_HALL_B = {"MOTOR_HALL_B", 10, INPUT};
const PinDef Pins::MOTOR_HALL_C = {"MOTOR_HALL_C", 11, INPUT};
const PinDef Pins::SENSOR_THROTTLE_DATA = {"SENSOR_THROTTLE_DATA", 34, INPUT};
const PinDef Pins::SENSOR_PAS_PULSE = {"SENSOR_PAS_PULSE", 35, INPUT};
const PinDef Pins::SENSOR_BRAKE_SIGNAL = {"SENSOR_BRAKE_SIGNAL", 32, INPUT_PULLUP};


void Pins::initPins() {
    // Initialize all pins modes
    pinMode(BATT_LEVEL.pin, BATT_LEVEL.mode);
    pinMode(MOTOR_ENABLE.pin, MOTOR_ENABLE.mode);
    pinMode(MOTOR_INHA.pin, MOTOR_INHA.mode);
    pinMode(MOTOR_INLA.pin, MOTOR_INLA.mode);
    pinMode(MOTOR_INHB.pin, MOTOR_INHB.mode);
    pinMode(MOTOR_INLB.pin, MOTOR_INLB.mode);
    pinMode(MOTOR_INHC.pin, MOTOR_INHC.mode);
    pinMode(MOTOR_INLC.pin, MOTOR_INLC.mode);
    ledcSetup(0, 20000, 16);
    ledcSetup(1, 20000, 16);
    ledcSetup(2, 20000, 16);
    ledcSetup(3, 20000, 16);
    ledcSetup(4, 20000, 16);
    ledcSetup(5, 20000, 16);
    ledcAttachPin(MOTOR_INHA.pin, 0);
    ledcAttachPin(MOTOR_INHB.pin, 1);
    ledcAttachPin(MOTOR_INHC.pin, 2);
    ledcAttachPin(MOTOR_INLA.pin, 3);
    ledcAttachPin(MOTOR_INLB.pin, 4);
    ledcAttachPin(MOTOR_INLC.pin, 5);
    pinMode(MOTOR_SOA.pin, MOTOR_SOA.mode);
    pinMode(MOTOR_SOB.pin, MOTOR_SOB.mode);
    pinMode(MOTOR_SOC.pin, MOTOR_SOC.mode);
    adcAttachPin(BATT_LEVEL.pin);
    adcAttachPin(MOTOR_SOA.pin);
    adcAttachPin(MOTOR_SOB.pin);
    adcAttachPin(MOTOR_SOC.pin);
    pinMode(MOTOR_HALL_A.pin, MOTOR_HALL_A.mode);
    pinMode(MOTOR_HALL_B.pin, MOTOR_HALL_B.mode);
    pinMode(MOTOR_HALL_C.pin, MOTOR_HALL_C.mode);
    attachInterrupt(digitalPinToInterrupt(MOTOR_HALL_A.pin), Motor::onHallChange, CHANGE);
    attachInterrupt(digitalPinToInterrupt(MOTOR_HALL_B.pin), Motor::onHallChange, CHANGE);
    attachInterrupt(digitalPinToInterrupt(MOTOR_HALL_C.pin), Motor::onHallChange, CHANGE);
    pinMode(MOTOR_FAULT.pin, MOTOR_FAULT.mode);
    attachInterrupt(digitalPinToInterrupt(MOTOR_FAULT.pin), DRV8353::checkFault, CHANGE);
    pinMode(SENSOR_THROTTLE_DATA.pin, SENSOR_THROTTLE_DATA.mode);
    pinMode(SENSOR_PAS_PULSE.pin, SENSOR_PAS_PULSE.mode);
    attachInterrupt(digitalPinToInterrupt(SENSOR_PAS_PULSE.pin), Motor::onPasPulse, RISING);
    pinMode(SENSOR_BRAKE_SIGNAL.pin, SENSOR_BRAKE_SIGNAL.mode);
    attachInterrupt(digitalPinToInterrupt(SENSOR_BRAKE_SIGNAL.pin), Motor::BRAKE, FALLING);
}

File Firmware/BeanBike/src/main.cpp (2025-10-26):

#include <Arduino.h>
#include "globals.h"

Pins pins;
Motor motor;
UART uart;
DRV8353 drv8353;
Battery battery;
Config config;
void uartReceiveCommandTask(void *pvParameters) {
  while (true) {
    uart.receiveCommand();  // Poll for commands
    vTaskDelay(10 / portTICK_PERIOD_MS);
  }
}

void setup() {
  pins.initPins();
  uart.init();
  drv8353.init();
  battery.updateBatteryStatus();
  xTaskCreatePinnedToCore(
    uartReceiveCommandTask, 
    "UARTReceive",    
    2048,         
    NULL,           
    1,        
    NULL,            
    0   
  );
}



void loop() {
  motor.CalculateSpeed();
  motor.updateCruiseControl();
  motor.updatePASControl();
  motor.updateThrottleControl();
  battery.updateBatteryStatus();
}

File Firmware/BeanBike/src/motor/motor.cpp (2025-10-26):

#include <Arduino.h>
#include <cmath>
#include "motor.h"
#include "globals.h"

int hallEdgeCount = 0;
const int PULSES_PER_MECH_REV = 138; // Adjust as needed to make accurate
const int SAMPLE_MS = 100;

constexpr uint32_t PAS_ACTIVITY_TIMEOUT_US = 600000; // 0.6 s without pulses = not pedaling
constexpr float PAS_ASSIST_RATIOS[] = {0.0f, 0.25f, 0.4f, 0.6f, 0.8f, 1.0f};
constexpr int PAS_MAX_LEVEL = (sizeof(PAS_ASSIST_RATIOS) / sizeof(PAS_ASSIST_RATIOS[0])) - 1;

volatile uint32_t pasPulseCount = 0;
volatile uint32_t lastPasPulseMicros = 0;

float readAdcVoltage(const PinDef& pin) {
    if (config.adcResolutionBits <= 0 || config.adcReferenceVoltage <= 0.0f) {
        return 0.0f;
    }

    static bool resolutionConfigured = false;
    if (!resolutionConfigured) {
        analogReadResolution(config.adcResolutionBits);
        resolutionConfigured = true;
    }

    const int raw = analogRead(pin.pin);
    const float maxCount = static_cast<float>((1 << config.adcResolutionBits) - 1);
    if (maxCount <= 0.0f) {
        return 0.0f;
    }

    return (static_cast<float>(raw) / maxCount) * config.adcReferenceVoltage;
}

float readPhaseCurrentAmps(const PinDef& pin) {
    const float shuntOhms = config.shuntResistanceMilliOhm * 0.001f;
    if (shuntOhms <= 0.0f || config.currentSenseGain <= 0.0f) {
        return 0.0f;
    }

    const float voltage = readAdcVoltage(pin);
    const float senseVoltage = voltage - config.currentSenseOffsetVolt;
    const float current = senseVoltage / (config.currentSenseGain * shuntOhms);
    return current;
}

float readAveragePhaseCurrentMagnitude() {
    const float ia = fabsf(readPhaseCurrentAmps(Pins::MOTOR_SOA));
    const float ib = fabsf(readPhaseCurrentAmps(Pins::MOTOR_SOB));
    const float ic = fabsf(readPhaseCurrentAmps(Pins::MOTOR_SOC));
    return (ia + ib + ic) / 3.0f;
}

static int applyPowerLimit(Motor& m, int requestedPwm) {
    if (requestedPwm <= 0 || config.maxMotorWattage <= 0) {
        m.lastBusVoltage = 0.0f;
        m.lastElectricalPower = 0.0f;
        m.lastPhaseCurrent = 0.0f;
        uart.sendData("MOTOR_POWER_LIMIT_ACTIVE", "FALSE");
        return requestedPwm;
    }

    m.lastBusVoltage = battery.getBatteryVoltage();
    m.lastPhaseCurrent = readAveragePhaseCurrentMagnitude();
    m.lastElectricalPower = m.lastBusVoltage * m.lastPhaseCurrent;

    uart.sendData("MOTOR_BUS_VOLT", String(m.lastBusVoltage, 2));
    uart.sendData("MOTOR_PHASE_CURRENT", String(m.lastPhaseCurrent, 2));
    uart.sendData("MOTOR_POWER_W", String(m.lastElectricalPower, 1));

    if (m.lastElectricalPower <= static_cast<float>(config.maxMotorWattage)) {
        uart.sendData("MOTOR_POWER_LIMIT_ACTIVE", "FALSE");
        return requestedPwm;
    }

    const float limitRatio = static_cast<float>(config.maxMotorWattage) / m.lastElectricalPower;
    const float clampedRatio = constrain(limitRatio, 0.0f, 1.0f);
    const int limitedPwm = static_cast<int>(roundf(requestedPwm * clampedRatio));
    uart.sendData("MOTOR_POWER_LIMIT_ACTIVE", "TRUE");
    uart.sendData("MOTOR_POWER_LIMIT_PWM", String(limitedPwm));
    return limitedPwm;
}



static float updatePasCadence(Motor& m) {
    static uint32_t lastSampleMicros = 0;
    static uint32_t lastPulseCount = 0;

    uint32_t pulseCountSnapshot;
    noInterrupts();
    pulseCountSnapshot = pasPulseCount;
    interrupts();

    const uint32_t nowMicros = micros();
    if (lastSampleMicros == 0) {
        lastPulseCount = pulseCountSnapshot;
        lastSampleMicros = nowMicros;
        m.pasCadenceRpm = 0.0f;
        return m.pasCadenceRpm;
    }

    if (pulseCountSnapshot < lastPulseCount) {
        lastPulseCount = pulseCountSnapshot;
        lastSampleMicros = nowMicros;
        m.pasCadenceRpm = 0.0f;
        return m.pasCadenceRpm;
    }

    const uint32_t deltaCount = pulseCountSnapshot - lastPulseCount;
    const uint32_t deltaMicros = nowMicros - lastSampleMicros;

    if (deltaCount == 0 || deltaMicros == 0 || config.pasPulsesPerRev <= 0) {
        return m.pasCadenceRpm;
    }

    const float pedalRevs = deltaCount / static_cast<float>(config.pasPulsesPerRev);
    m.pasCadenceRpm = (pedalRevs * 60000000.0f) / static_cast<float>(deltaMicros);

    lastPulseCount = pulseCountSnapshot;
    lastSampleMicros = nowMicros;
    return m.pasCadenceRpm;
}

void Motor::onHallChange() {
    hallEdgeCount++;
}

void Motor::onPasPulse() {
    pasPulseCount++;
    lastPasPulseMicros = micros();
}


#pragma region Calculations
// Caluclations

static float wheelFactorMphPerRpm() {
    const float wheelDiameterInches = static_cast<float>(config.wheelDiameterInches);
    return (PI * wheelDiameterInches / 63360.0f) * 60.0f;
}
void Motor::CalculateSpeed(){
    static uint32_t lastCount = 0;
    static uint32_t lastSample = millis();

    uint32_t now = millis();
    if (now - lastSample < SAMPLE_MS) return;

    noInterrupts();
    uint32_t countSnapshot = hallEdgeCount;
    interrupts();

    uint32_t deltaCount = countSnapshot - lastCount;
    float intervalSec = (now - lastSample) / 1000.0f;
    float mechRevs = deltaCount / static_cast<float>(PULSES_PER_MECH_REV);
    rpm = (mechRevs / intervalSec) * 60.0f;

    uart.sendData("MOTOR_RPM", String(rpm));

    lastCount = countSnapshot;
    lastSample = now;
    mph = rpm * wheelFactorMphPerRpm();
    uart.sendData("MOTOR_SPEED_MPH", String(mph, 2));
}
static int clampPasLevel(int level) {
    return constrain(level, 0, PAS_MAX_LEVEL);
}

static bool pedalsAreMoving() {
    noInterrupts();
    const uint32_t lastPulseMicrosSnapshot = lastPasPulseMicros;
    const uint32_t pulseCountSnapshot = pasPulseCount;
    interrupts();

    if (pulseCountSnapshot == 0 || lastPulseMicrosSnapshot == 0) {
        return false;
    }

    const uint32_t nowMicros = micros();
    const uint32_t elapsed = nowMicros - lastPulseMicrosSnapshot;
    return elapsed <= PAS_ACTIVITY_TIMEOUT_US;
}

static int CalculateMotorPowerSpeed(float targetMph) {
    const float mphPerRpm = wheelFactorMphPerRpm();
    if (mphPerRpm <= 0.0f || config.maxMotorRPM <= 0.0f) {
        return 0;
    }

    const float targetRPM = targetMph / mphPerRpm;
    const float pwmRatio = constrain(targetRPM / config.maxMotorRPM, 0.0f, 1.0f);
    const int pwmValue = static_cast<int>(roundf(pwmRatio * ((1 << 16) - 1)));

    return pwmValue;
}
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

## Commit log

2025-10-10 Init Commit
    Just setup a KiCad project
    [Controller.kicad_pcb, Controller.kicad_sch, beanbike_controller.kicad_sch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]
2025-10-11 Power Circuit V1
    [Controller.kicad_sch, beanbike_power.kicad_sch]
2025-10-13 PCB v1
    Whole lotta stuff
    [Controller.kicad_pcb, Controller.kicad_sch, beanbike_controller.kicad_sch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]
2025-10-15 PCB v2
    [Controller.kicad_pcb, beanbike_controller.kicad_sch, beanbike_controller_12v.kicad_sch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]
2025-10-19 PCBv2 Finish
    [Controller.kicad_pcb, beanbike_controller.kicad_sch, beanbike_controller_3.3v.kicad_sch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]
2025-10-21 More Firmware
    😄
    [Controller.kicad_pcb, beanbike_controller.kicad_sch, beanbike_controller_connectors.kicad_sch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]
2025-10-21 FIRMWARE v1
    [Display.kicad_pcb, Display.kicad_sch]
2025-10-26 Finishing Things Up
    [BeanBike-BOM.csv, Controller.kicad_pcb, Controller.kicad_sch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]
2025-10-26 Finishing touches/Shipping
    [BeanBike-BOM.csv]
2025-11-03 Forgot to commit
    [Controller.kicad_sch, beanbike_controller.kicad_sch, beanbike_controller_3.3v.kicad_sch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]
2025-11-07 Schematic v3 Done
    [beanbike_controller.kicad_sch, beanbike_controller_motor.kicad_sch, beanbike_power.kicad_sch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]
2025-11-08 PCB v3
    [Controller.kicad_pcb, beanbike_controller.kicad_sch, beanbike_controller_connectors.kicad_sch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]
2025-11-09 Fix grammar and update BOM formatting in README
    Corrected grammar and punctuation in the README file, particularly in the 'Why?' section. Updated the BOM table formatting and content.
2025-11-09 Finish up
    [Display.kicad_pcb, Display.kicad_sch, bom.csv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]
2025-12-28 big ol update
    [Controller.kicad_pcb, Controller.kicad_sch, beanbike_controller.kicad_sch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]
